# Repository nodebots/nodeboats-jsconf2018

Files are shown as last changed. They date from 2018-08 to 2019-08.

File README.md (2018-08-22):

# Welcome to NodeBoats at JS Conf 2018!

### Getting Started

As part of this workshop, you should divide up into teams of 3-4 people. Try to find people with a similar boat "vision" as you to partner with.

Teams will be building a motor-propelled boat, which will require some soldering. Feel free to ask any of the workshop team members if you need help with any part of this process.

Each boat kit will include the following materials. Make sure you let us know if any components are missing! (Please also keep in mind that we do need the parts back at the end of the day!)

#### Boat Kits

- Arduino Nano
- Electronic Speed Controller (ESC) 30A with Reverse
- Micro Servo
- HC-06 Bluetooth Module
- 2S Lipo Battery with XT60 connector
- 2S USB Lipo Charger
- Breadboard
- USB A <-> Mini-B USB cable
- Jumper Wires (Male-to-Male && Female-to-Male)
- Wire Extension
- Brushless Motor
- Propellor
- L-shaped connector
- Boat Hull (aka Plastic Takeout Boxes)

#### Things you may need (And We Have!!!)

- Goopy goo glue sealant
- Styrofoam (we have sheets and will cut off what your boat needs)
- Popsicle Sticks!
- Hot glue gun
- Soldering irons & solder
- Heat shrink tubing & heaters
- Wire cutters/strippers
- A drill
- Box cutters
- Googly eyes
- Feathers
- Mini Pool Floaties

### Configuring the Arduino Nano & HC-06 Bluetooth module

To avoid using extemely long USB cables to drive the boats from the water to your laptops, the HC-06 Bluetooth module will allow you to run Johnny-Five commands wirelessly to the Arduino Nano. The NodeBoats team has pre-configured the modules to do this, so the following instructions are useful if you are building the boat at home later or need to reconfigure the module. They are based on the [HC-05 configuration docs](https://github.com/rwaldron/johnny-five/wiki/Getting-Started-with-Johnny-Five-and-HC-05-Bluetooth-Serial-Port-Module) with some key changes for the HC-06 and this workshop.

**For the workshop, you can [skip to steps 4 and 5](https://github.com/opheliasdaisies/nodeboats-jsconf2018#step-4-wire-the-module-to-the-arduinos-hardware-port) to learn about pairing the pre-configured module with your laptop.**

#### Step 1: Connect the HC-05 module to the Arduino for configuration

We will program the Arduino to send AT commands to the module to configure it via a SoftwareSerial connection. Wire the TX (transmit) and RX (receive) pins of your module to your Arduino. They need to be wired in a crossover configuration, so from the module to the Arduino wire TX to pin 10 and RX to pin 11. (For the purpose of configuring the Bluetooth module, pin 10 is used as RX on the Arduino, and pin 11 is used as TX. Later, when running Johnny-Five code, we'll use the pins labeled TX and RX on the arduino.)

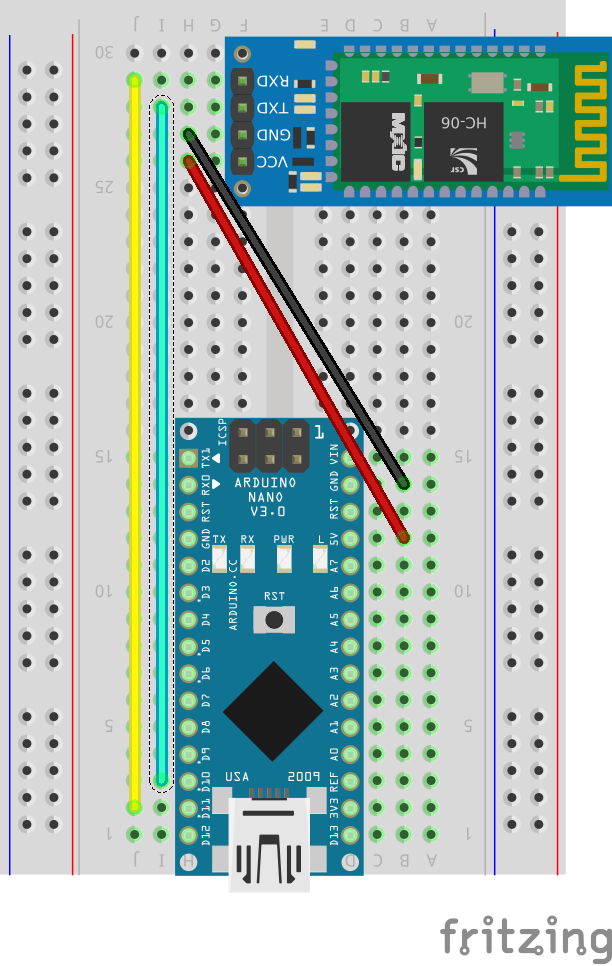
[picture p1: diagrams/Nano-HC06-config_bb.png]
Arduino Nano to HC-06 Bluetooth breadboard


You will need the [Arduino IDE](https://www.arduino.cc/en/main/software) to upload the [configuration sketch file](/code/HC06-Config/HC06-Config.ino) to your Arduino. The sketch will create a connection between the Arduino's serial port and the HC-06, as well as configure the HC-06 to use the same [baudrate](https://en.wikipedia.org/wiki/Baud) as Johnny-Five.o

```c

  // Set ROBOT_NAME to something unique
  #define ROBOT_NAME "RandomBot"

  // If you haven't configured your device before use this
  #define BLUETOOTH_SPEED 9600 //This is the default baudrate that HC-06 uses
  // If you are modifying your existing configuration, use this:
  // #define BLUETOOTH_SPEED 57600

  #include <SoftwareSerial.h>

  // Swap RX/TX connections on bluetooth chip
  //   Pin 10 --> Bluetooth TX
  //   Pin 11 --> Bluetooth RX
  SoftwareSerial mySerial(10, 11); // RX, TX

  /*
    The possible baudrates are:
      AT+UART=1200,0,0 -------1200
      AT+UART=2400,0,0 -------2400
      AT+UART=4800,0,0 -------4800
      AT+UART=9600,0,0 -------9600 - Default for hc-06
      AT+UART=19200,0,0 ------19200
      AT+UART=38400,0,0 ------38400
      AT+UART=57600,0,0 ------57600 - Johnny-five speed
      AT+UART=115200,0,0 -----115200
      AT+UART=230400,0,0 -----230400
      AT+UART=460800,0,0 -----460800
      AT+UART=921600,0,0 -----921600
      AT+UART=1382400,0,0 ----1382400
  */

  void setup() {
    Serial.begin(9600);

    Serial.println("Starting config");
    mySerial.begin(BLUETOOTH_SPEED);
    delay(1000);

    // Should respond with OK
    mySerial.print("AT\r\n");
    waitForResponse();

    // Should respond with its version
    mySerial.print("AT+VERSION\r\n");
    waitForResponse();

    // Should respond with default password, probably 1234
    mySerial.print("AT+PSWD\r\n");
    waitForResponse();

    // Set the name to ROBOT_NAME
    String rnc = String("AT+NAME=") + String(ROBOT_NAME) + String("\r\n"); 
    mySerial.print(rnc);
    waitForResponse();

    // Set baudrate to 57600
    mySerial.print("AT+UART=57600,0,0\r\n");
    waitForResponse();

    Serial.println("Done!");
  }

  void waitForResponse() {
      delay(1000);
      while (mySerial.available()) {
        Serial.write(mySerial.read());
      }
      Serial.write("\n");
  }

  void loop() {}

```

#### Step 2: Check configuration

The setup() function will take about 6 seconds to run. You can connect to the Arduino with Serial Monitor and you should see the following output.

```

  Starting config
  OK
  OK[VERSION]
  OK[PSWD]
  OK
  OK
  Done!

```

If you saw that, congratulations! You're done with this step.

If you see the following output instead, you will probably have to change BLUETOOTH_SPEED to another value and upload it again. This could be because the HC-06 chip had a different baud rate.

```

  Starting config

  Done!

```

If you are having trouble uploading the firmata firmware to the device, make sure that nothing is connected to pins 0 and 1 when uploading, as this can interfere with the upload process.

#### Step 3: Re-upload StandardFirmataPlus

Once the baud rate is properly set, re-upload the StandardFirmataPlus sketch to your board. If you don't do this it might seem that your bluetooth module is getting a connection and the light will stop blinking, but you won't be able to connect.

You can upload StandardFirmataPlus through the [Arduino IDE](https://www.instructables.com/id/Arduino-Installing-Standard-Firmata/) or using [firmata-party](https://www.npmjs.com/package/firmata-party) from the command line.

#### Step 4: Wire the module to the Arduino's hardware port

Once the baud rate is properly set & Firmata reloaded, which has already been done for you for the workshop, connect the TX and RX pins to Arduino pins RX0 and TX1 respectively.

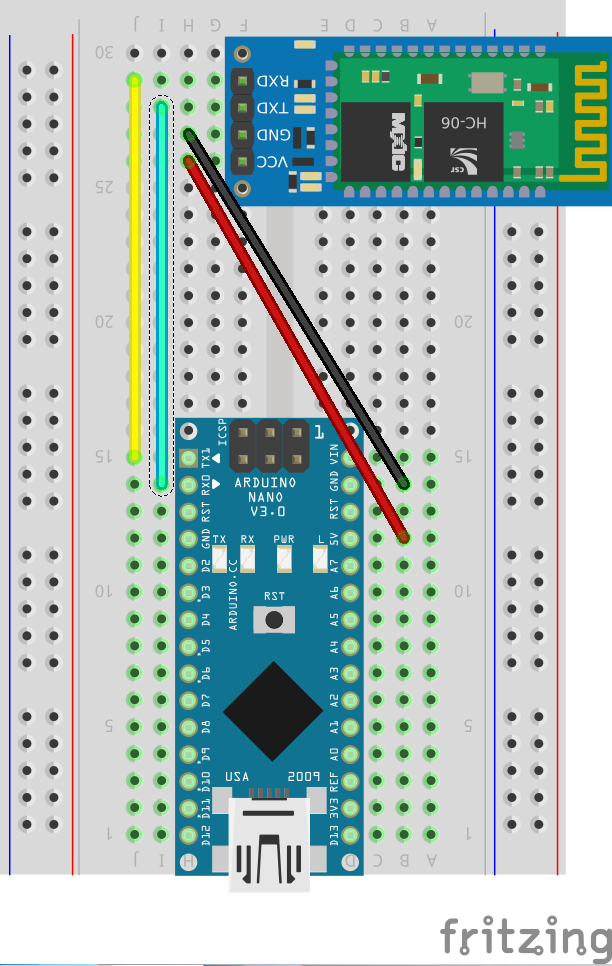
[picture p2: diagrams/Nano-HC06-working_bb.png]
Arduino Nano to HC-06 hookup


#### Step 5: Pair the module

Pair to the module from your host device. Once you have paired with your bluetooth device the serial port should be visible with the 'ROBOT_NAME' used in Step 1. (If you're in the workshop at JS Conf, the 'ROBOT_NAME' will be labeled on your module when you receive it, and the pin code will be 1234.) It will be something like /dev/tty.ROBOT_NAME-SPPDev (in UNIX) and use COMX in Windows (where X is the number of the port). Use this name to tell [Johnny-Five which port to use](http://johnny-five.io/api/board/#component-initialization).

You can test the connection by modifying the `blink.js` program to add the path to the Bluetooth port and running the program. Make sure Johnny-Five is installed in the `code` directory (`npm install`) before running `node code/blink.js`. 

### Resources for Building Your Boat!

You may need some help while setting up your NodeBoat. Here are some tips and tricks so you can learn from our experiences:

- Check out the [build guide](./build.md) to see wiring examples and tips for working with the ESC and servo.
- The [Arduino Nano pinout](http://www.circuitstoday.com/arduino-nano-tutorial-pinout-schematics) is a handy reference for what each pin can do
- The name of the Bluetooth module should be on its bag, look for this when pairing it with your laptop
- Connect the ground (GND) wire before connecting the power wire, especially when working with the lipo battery.
- Unplugging or turning off power when switching wires is good practice to avoid unexpected short circuits.

First Time Using Johnny-Five? Don't hesitate to ask us for help! That's why we're here. Here are some intro materials and parts of the docs that will be particularly helpful while building your boats:

- [Board class API](http://johnny-five.io/api/board/#component-initialization)
- [ESC class API](http://johnny-five.io/api/esc/)
- [Servo class API](http://johnny-five.io/api/servo/)
- [Controlling Johnny-Five with `keypress`](https://gist.github.com/goldsamantha/1fd9ba71c398e8a06fd319cac05cf022)
- [Controlling Johnny-Five with Express & Socket.io](https://learn.sparkfun.com/tutorials/reconbot-with-the-tessel-2)

### Examples

These are a few examples of boats that the Nodeboats Team has built to show the variety of design and creativity that can go into creating your vessel.

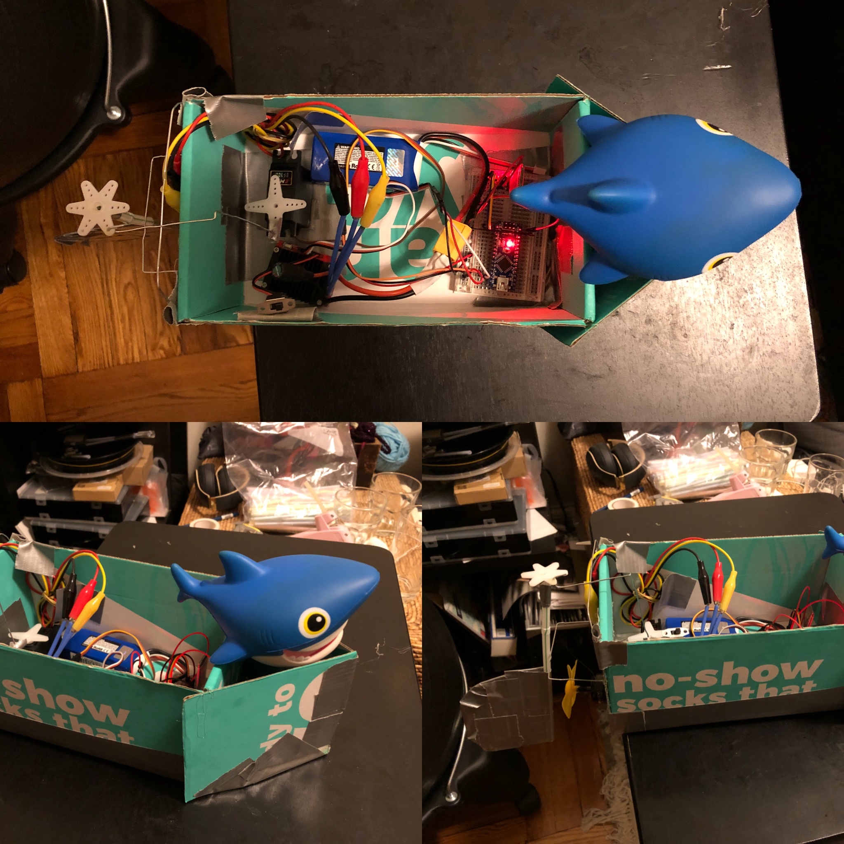
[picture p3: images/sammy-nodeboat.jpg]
Captain Sammy


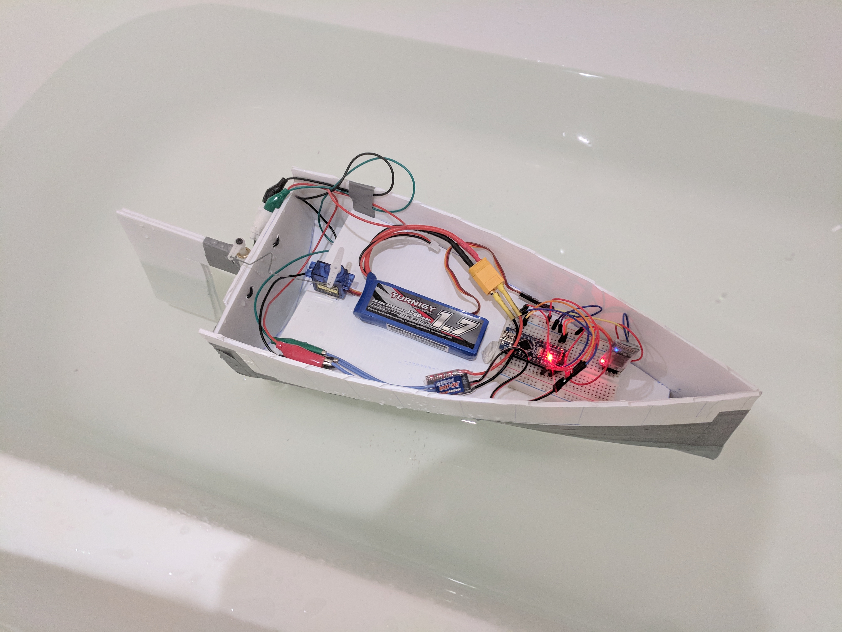
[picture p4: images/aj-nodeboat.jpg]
AJ Nodeboat


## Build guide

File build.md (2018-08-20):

# Tips for Building The Motor-powered Nodeboat!

This build does require soldering, so ask for help if you need it.

In order to power the boat, the battery will connect directly to the Electronic Speed Controller (ESC) and share the power from the ESC to the breadboard. See the hookup diagram below. The battery has an XT60 connector that needs a matching connector soldered onto the ESC's red and black wires. Check out the sides of the XT60 for a plus (+) and a minus (-) sign with the red wire (power) lining up with the plus sign and the black wire (ground) lining up with the minus sign. Once the battery is hooked up to the ESC, you can use the power switch on the ESC to test the connection.

The following is an example hookup for using the ESC:
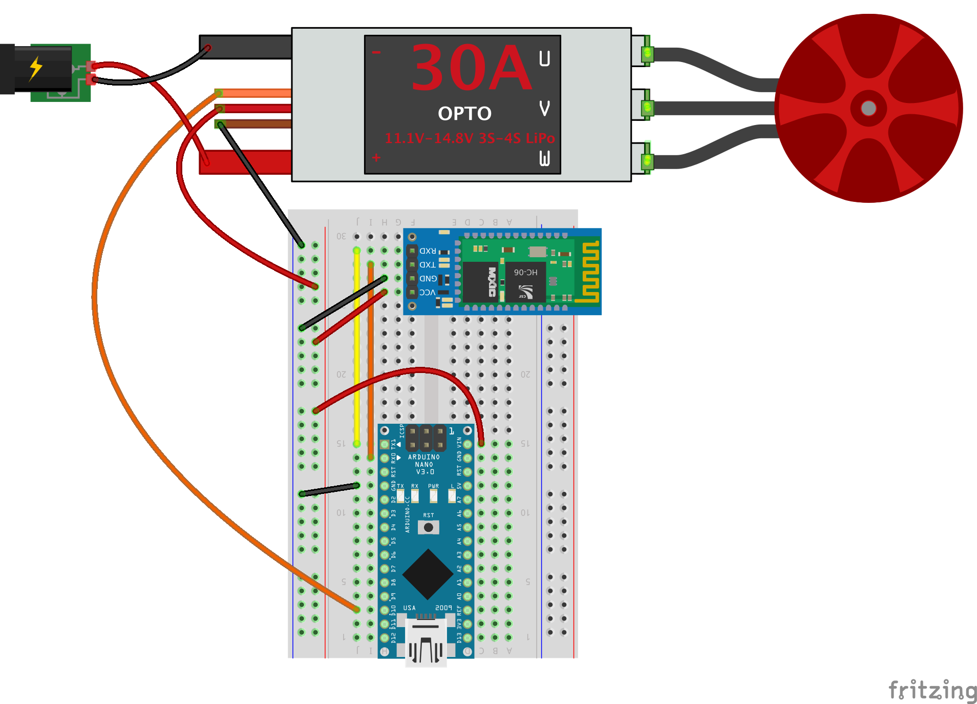
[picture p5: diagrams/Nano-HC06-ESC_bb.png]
Arduino Nano to ESC hookup


Pin hookup:

- RXD on HC-06 <-> TX1 on Nano
- TXD on HC-06 <-> RX0 on Nano
- Orange wire on ESC <-> D10 on Nano
- Every black wire goes to the ground (GND) rail
- Every red wire, VCC on HC-06, and VIN on Nano goes to the power rail

Adding the servo for steering is as simple as adding three more wires to the breadboard:
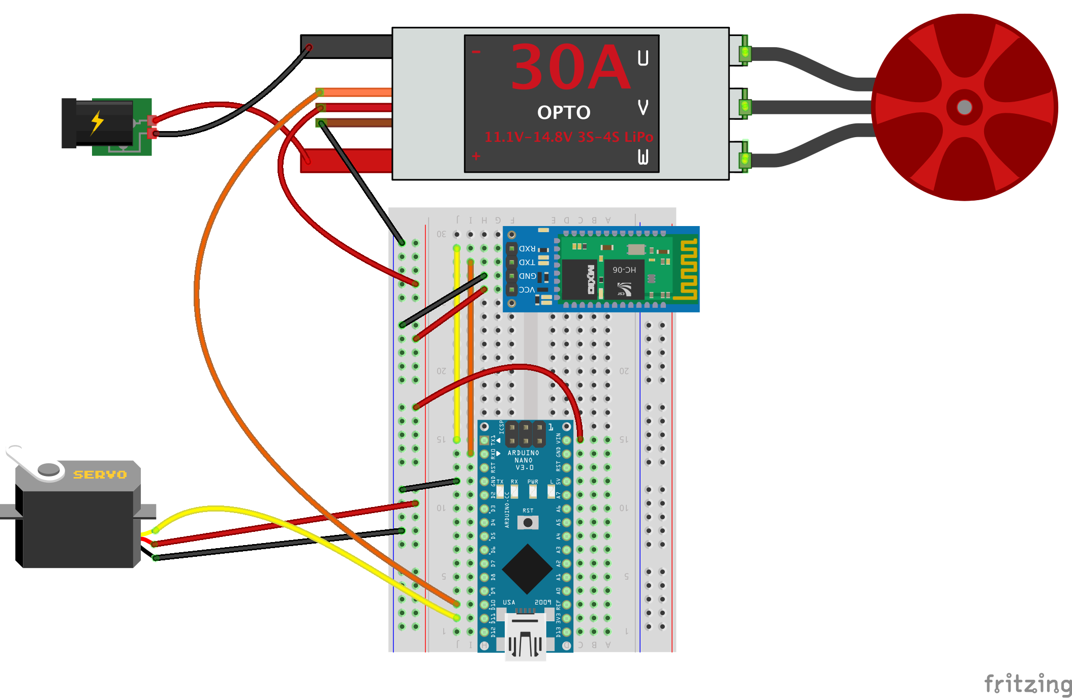
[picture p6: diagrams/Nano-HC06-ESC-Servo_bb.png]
Arduino Nano with ESC and Servo hookup


Pin hookup:

- RXD on HC-06 <-> TX1 on Nano
- TXD on HC-06 <-> RX0 on Nano
- Orange wire on ESC <-> D10 on Nano
- **Yellow wire on Servo <-> D11 on Nano**
- Every black wire goes to the ground (GND) rail
- Every red wire, VCC on HC-06, and VIN on Nano goes to the power rail

The L-shaped connector included in the kit can be used as a rudder and/or mount for the motor. This can be attached with one end on the top of the servo and the other end attached to the back of the motor, or the motor can be fastened to the boat and the L-connector can be used to fashion a rudder connected to the servo. You can use glue, duct tape, or whatever method you'd like for attaching and modifying it. Or you can come up with some other configuration entirely. Let your boat be its true self!

## Wiring Tips

- You may notice the 5V pin on the Arduino Nano is not powering the HC-06 or any other device. This is to prevent [brownouts](https://en.wikipedia.org/wiki/Brownout_(electricity)) that can be caused by spikes in power draw from the servo or motor.

## General Tips

- Before drilling a hole in the boat hull to pass through the wires from the motor pod, it is strongly recommended that you put all of your components in the boat first, to test the bouyancy and add the appropriate amount of styrafoam to the boat.
- If you drill a hole in your boat hull that could possibly be submerged, make sure you seal it well! After your wires are properly positioned through the hole, apply waterproof sealant to both sides of the hole and allow it to dry before testing it in the water.
- Servos are not waterproof! Make sure to keep them out of the water!
- The motors we're using are [brushless motors](https://www.renesas.com/us/en/support/technical-resources/engineer-school/brushless-dc-motor-01-overview.html) and can go underwater, like magic! Don't worry about submerging these, but also know that standard brushed motors can't be.
- If you need to extend any jumper wires, we have heat shrink tubing which can form a watertight seal and help you join them.

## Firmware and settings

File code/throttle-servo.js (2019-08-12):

const {Board, ESC, Fn, Led, Servo} = require('johnny-five');
const keypress = require('keypress');

const board = new Board({
  port: '', // path to bluetooth connection, i.e. /dev/tty.ROBOT_NAME-SPPDev or COMX
});

board.on('ready', () => {
  const led = new Led(13);
  const esc = new ESC({
    device: 'FORWARD_REVERSE',
    pin: 11,
  });
  const servo = new five.Servo(10);
  let speed = 0;
  let last = null;

  servo.center();

  // just to make sure the program is running
  led.blink(500);

  function controller(_, key) {
    let change = 0;

    if (key) {
      if (!key.shift) {
        change = esc.neutral;
        speed = 0;
      } else {
        if (key.name === 'up' || key.name === 'down') {
          if (last !== key.name) {
            change = esc.neutral;
            speed = 0;
          } else {
            speed += 1;

            change =
              key.name === 'up' ? esc.neutral + speed : esc.neutral - speed;
          }
          last = key.name;
        }

        if (key.name === 'left') {
          servo.to(45, 1000);
        }

        if (key.name === 'right') {
          servo.to(135, 1000);
        }

        if (key.name === 'c') {
          servo.center();
        }
      }

      if (change) {
        esc.throttle(change);
      }
    }
  }

  keypress(process.stdin);

  process.stdin.on('keypress', controller);
  process.stdin.setRawMode(true);
  process.stdin.resume();
});

board.on('error', error => {
  console.error(error);
  process.exit(1);
});

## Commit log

2018-08-13 initial documentation
    [Nano-HC06-ESC-Servo.fzz, Nano-HC06-ESC.fzz, Nano-HC06-config.fzz]
2018-08-22 Add workshop pin code to pairing directions
2019-08-12 Update johnny-five, include throttle, servo examples
